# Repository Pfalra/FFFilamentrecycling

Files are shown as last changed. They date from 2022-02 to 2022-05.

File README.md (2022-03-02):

# FFFilamentrecycling

Hello there! This thing is still work in progress. We aim to create a filament converter from 3mm to 1.75mm filament... at least in the short term. In the long term our goal is to design just another filament recycling device that will crack your messed up prints, bottles and any other plastic thing you feed it with.
The mechanical parts are based on the master thesis of one of our contributors. Maybe we will publish his work here too.

Main electronics of our project are a ESP32-WROOM and a MAX10 FPGA reading a CCD sensor. The rest is currently pretty much neglectable as in the future we will integrate everything neatly onto a beautiful PCB instead of the current setup with its off-the-shelf Arduino modules and loads of jumper wire.

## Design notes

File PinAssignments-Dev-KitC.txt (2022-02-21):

INPUTS ONLY:
GPIO34
GPIO35
GPIO36
GPIO39

PINS WITH INTERNAL PULL UP:
GPIO14
GPIO16
GPIO17
GPIO18
GPIO19
GPIO21
GPIO22
GPIO23

PINS WITHOUT INTERNAL PULL UP:
GPIO13          x
GPIO25          x
GPIO26          x
GPIO27          x
GPIO33          x

SERIAL PINS:
GPIO3 (U0RXD) // DEBUG
GPIO1 (U0TXD) // DEBUG

GPIO16 (U2RXD)  x
GPIO17 (U2TXD)  x

I²C:
GPIO21 (SDA)    x
GPIO22 (SCL)    x

VSPI:
GPIO23 (MOSI)   x
GPIO19 (MISO)   x
GPIO18 (CLK)    x
GPIO5 (CS)      x

HSPI:
GPIO13 (MOSI)
GPIO12 (MISO) // Boot fail if pulled high
GPIO14 (CLK) // PWM at boot
GPIO15 (CS) // PWM at boot

BOOTSTRAP PINS:
GPIO0 (DEFAULT PUP) 
GPIO2 (DEFAULT PDOWN)
GPIO5 (DEFAULT PUP) // Outputs PWM at Boot

-----------------------------------------------
ASSIGNMENTS:
FPGA UART-RX    -> GPIO17 v
FPGA UART-TX    -> GPIO16 v

Heater          -> GPIO33 v

SD SPI-SCK      -> GPIO14 v
SD SPI-CS       -> GPIO15 v
SD SPI-MISO     -> GPIO12 v
SD SPI-MOSI     -> GPIO13 v

ADC/OLED I²C-SDA    -> GPIO21   v
ADC/OLED I²C-SCL    -> GPIO22   v

Stepper EN          -> GPIO27 v
ExtStepper STEP     -> GPIO26 v
PullStepper STEP    -> GPIO25 v
WinchStepper STEP   -> GPIO33 v

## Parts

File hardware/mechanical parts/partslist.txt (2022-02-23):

parts list
1. 1x fully assembled All-Metal Hotend Bowden - 3,00 mm
2. 2x MINEBA stepper motor 17PM-K374BN01CN, 1,8°
3. 1x extruder connector
4. 1x extruder mount
5. 1x extrouder mount counterpart 
6. 1x Anself Ultra-quiet Mini DC12V 4.5W Micro Brushless Water Oil Pump
7. 1x PVC tube 9mm
8. 1x PVC tube 6mm
9. 1x tube coupling
10. 1x basin
11. 1x basin cover
12. 1x inlet tube
13. 1x outlet tube
14. 1x MAX1000 - IoT Maker Board 16 kLE, 32 MByte SDRAM
15. 1x Toshiba TCD132D CCD
16. 1x Laser diode 5mW red 650nm 5V
17. 2x 6x24x9mm u-groove bearing
18. 1x 6mm round bar
19. 1x measuring device base
20. 1x measuring device housing
21. 2x bearing mount
22. 2x measuring device spacer
23. 1x FPGA cover
24. 1x laser mount 
25. 2x 6x19x6mm bearing 
26. 1x filament puller connector
27. 1x motor mount
28. 1x motor mount counterpart
29. 2x pull roll
30. 1x filament puller driven gear M=2,5 Z=20 
31. 1x filament puller gear M=2,5 Z=20 
32. 1x motor gear connector
33. 1x MINEBA stepper motor 17PM-K077BP01CN, 1,8°
34. 1x 12mm tube 
35. 1x filament winder driven gear M=2,5 Z=14
36. 1x filament winder gear M=2,5 Z=38
37. 1x filament winder gear counterpart
38. 1x filament winder tube connector
39. 1x filament winder base
40. 1x filament winder stepper motor mount
41. 1x filament winder stepper motor mount counterpart
42. 1x ESP32-Wroom DevKit
43. 1x ADS1115 ADC-Module (HW196)
44. 1x Micro SD-Module (HW125)
45. 1x Voltage Translator Joy-It KY-061
46. 3x A4988 StepStick
47. 1x IRFZ44N MOSFET
48. 3x 47µF Capacitor
49. 1x I^2C OLED Display
50. 1x 100k NTC
51. 2x M2,5 nylon nut DIN934 
52. 2x M2,5 nylon bolt
53. 2x M2 nylon nut DIN934 
54. 2x M2 nylon bolt
55. 8x M3 nut DIN934 
56. 16x M3 bolt 
57. 8x M4 nut DIN934 
58. 8x M4 bolt

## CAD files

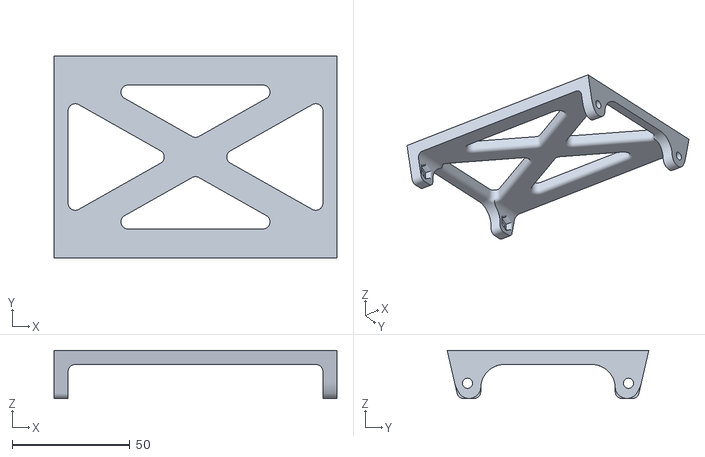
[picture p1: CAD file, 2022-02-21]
hardware/mechanical parts/Grundplatte_Rollenhalter.stl
120.0 x 85.6 x 20.5

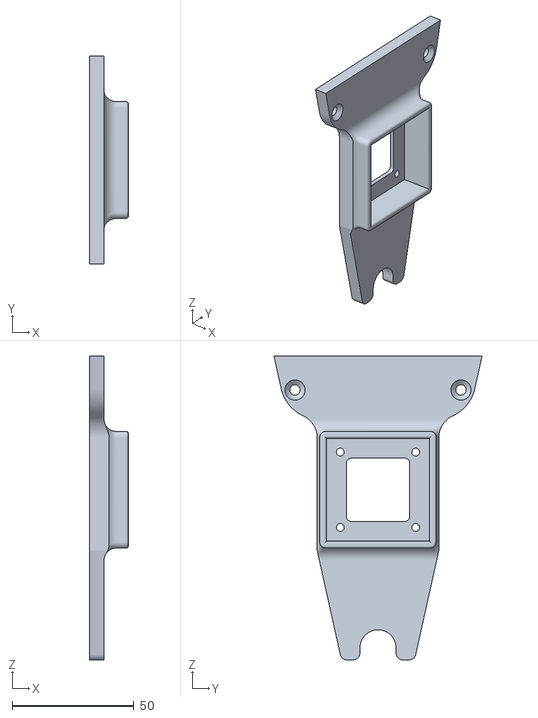
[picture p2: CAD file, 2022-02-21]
hardware/mechanical parts/Halter_Motorseitig.stl
16.0 x 85.6 x 125.0

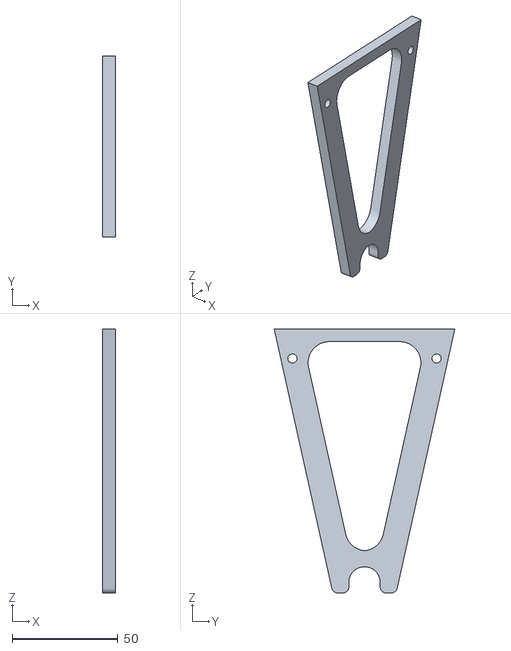
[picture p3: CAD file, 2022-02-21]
hardware/mechanical parts/Halter_Frei.stl
6.00 x 85.6 x 125.0

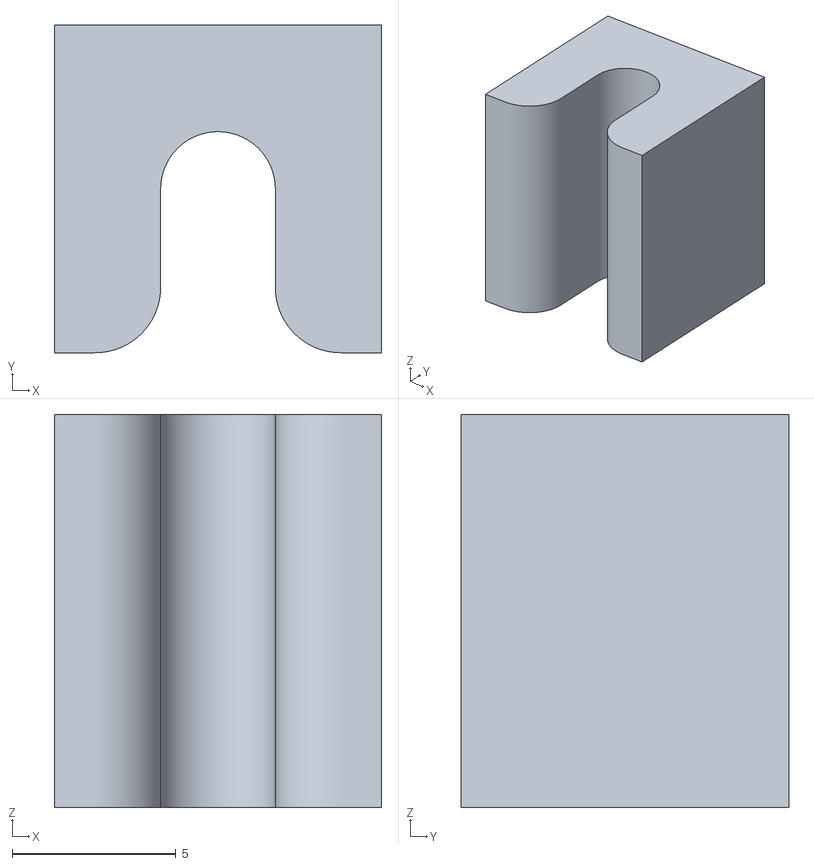
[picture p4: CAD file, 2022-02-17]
hardware/mechanical parts/Distanzstueck.stl
10.00 x 10.0 x 12.0

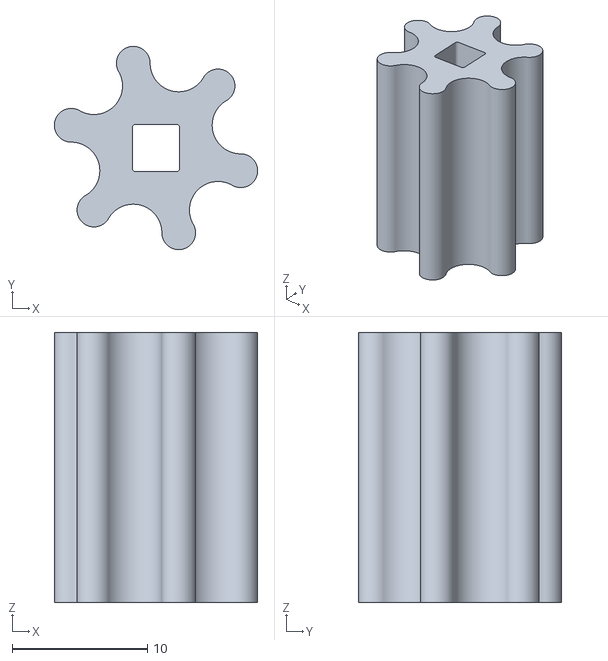
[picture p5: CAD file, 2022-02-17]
hardware/mechanical parts/Kraftschluss Zahnradantrieb.stl
15.1 x 15.1 x 20.0

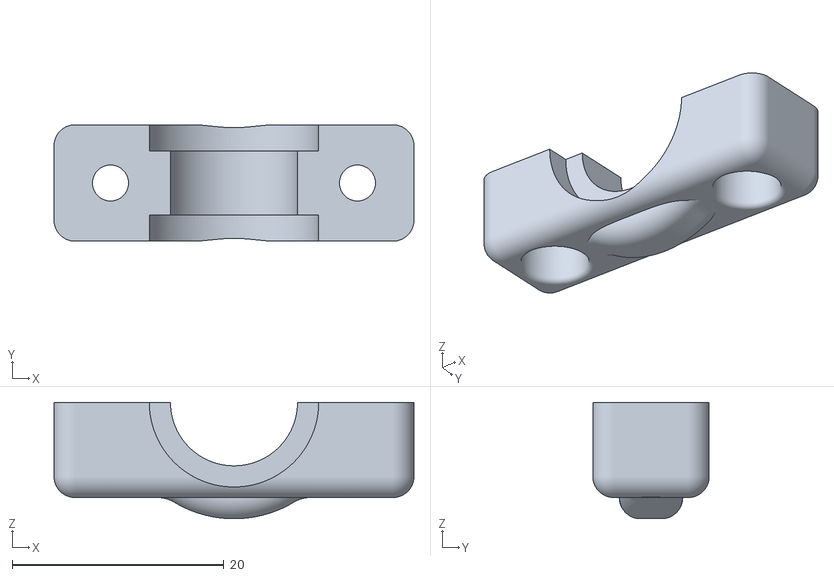
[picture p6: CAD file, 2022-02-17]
hardware/mechanical parts/Gegenstueck Halter.stl
34.0 x 11.0 x 11.0

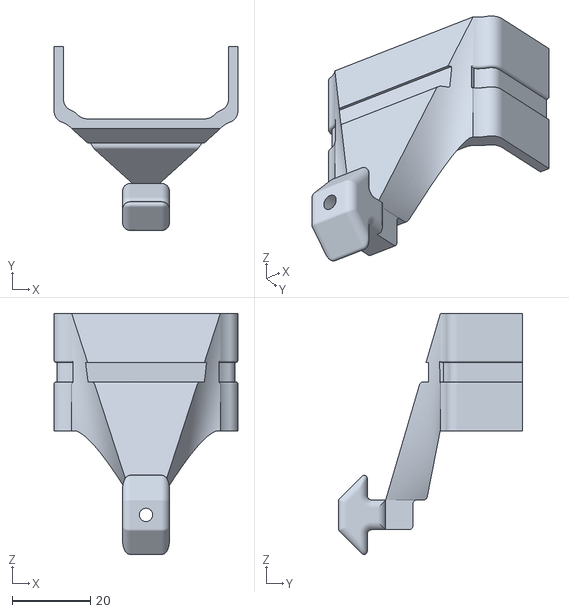
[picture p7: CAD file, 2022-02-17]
hardware/mechanical parts/Extruderhalter.stl
47.0 x 47.0 x 61.6

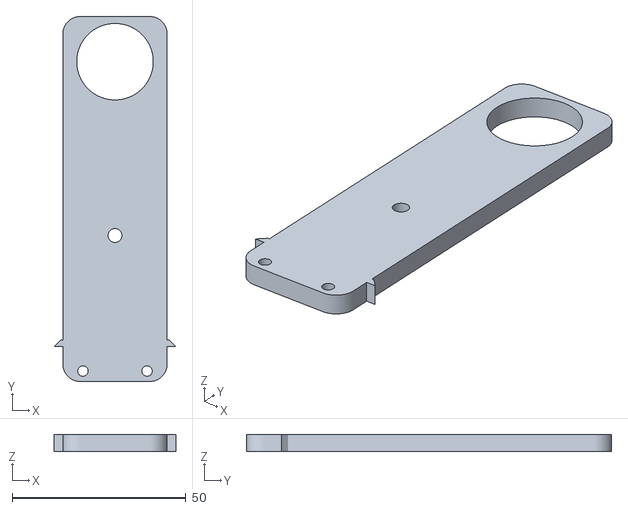
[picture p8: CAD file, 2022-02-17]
hardware/mechanical parts/Motorhalter Gegenstueck.stl
35.0 x 105.0 x 5.00

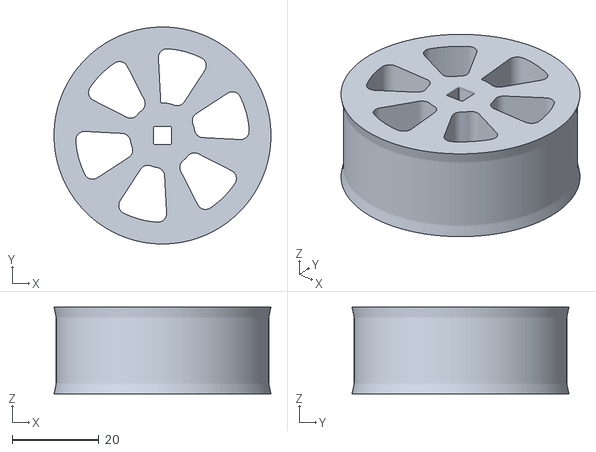
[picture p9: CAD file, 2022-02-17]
hardware/mechanical parts/Ziehrolle.stl
50.0 x 50.0 x 20.0

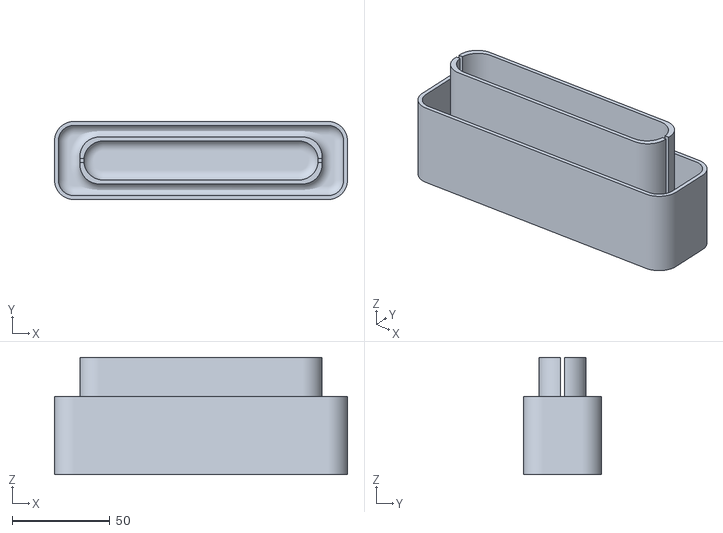
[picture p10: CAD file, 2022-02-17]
hardware/mechanical parts/Wasserbecken.stl
150.0 x 40.0 x 60.0

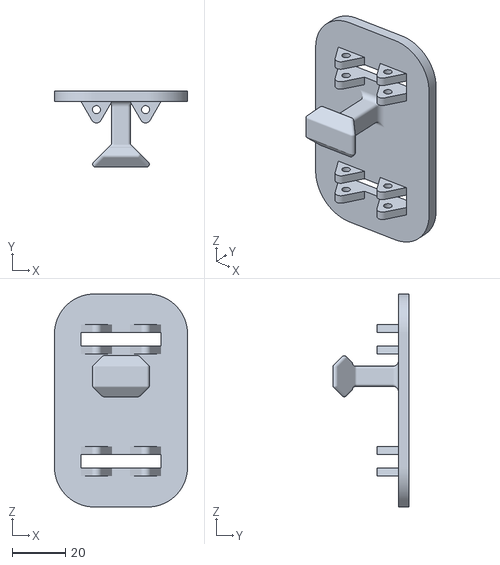
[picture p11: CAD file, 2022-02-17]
hardware/mechanical parts/Grundplatte Item.stl
50.0 x 28.5 x 80.0

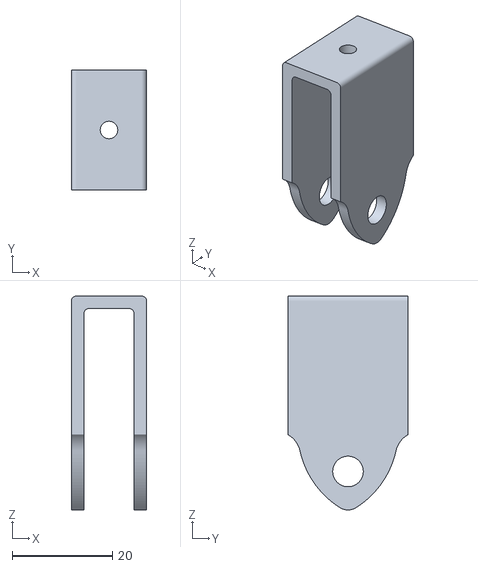
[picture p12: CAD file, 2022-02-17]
hardware/mechanical parts/Kugellagerhalter.stl
15.0 x 24.0 x 42.7

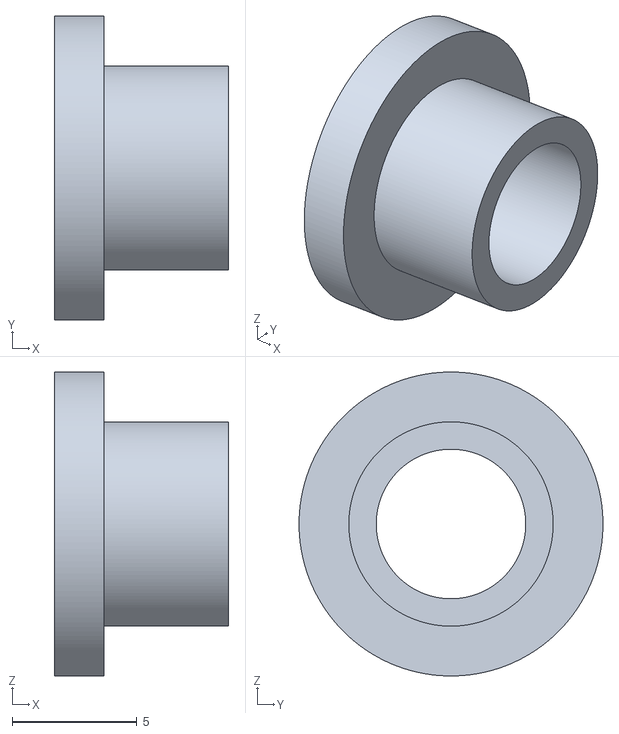
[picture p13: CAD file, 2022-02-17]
hardware/mechanical parts/Kugellageradapter.stl
7.00 x 12.2 x 12.2

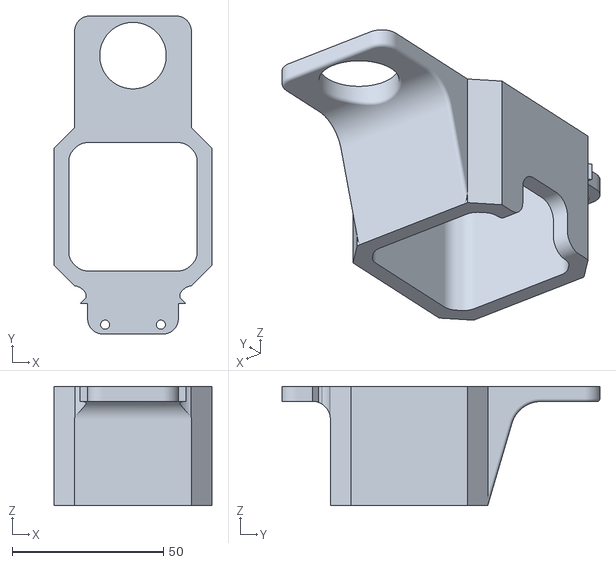
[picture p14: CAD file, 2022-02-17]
hardware/mechanical parts/Motorhalter.stl
52.2 x 105.2 x 39.4

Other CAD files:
FPGA/FilamentSensor/stp.stp
hardware/mechanical parts/Halterplatte.stl
hardware/mechanical parts/Wasserablauf.stl

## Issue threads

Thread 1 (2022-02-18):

UDP runtime error

Pfalra, 2022-02-18:
The udp stack prints an error while listening to the assigned port.
Maybe stack size for the corresponding task is insufficient.

g3gg0, 2022-02-18:
got comparable issues while using ArduinoOTA in some other project.
Stack trace showed the new() call within some UDP receive code was failing.

not sure what causes that.

Pfalra, 2022-02-19:
Up until now we used the Wemos Lolin32. Somehow this error does not occur when the code is running on the ESP32-Wroom DevKit. I just switched the board and additionally to being functional now, we have more pins we can use.

Closed 2022-02-19.

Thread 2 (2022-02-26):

Device cannot be flashed if external modules are powered

Pfalra, 2022-02-26:
Module must be identified and connected to other pins.

Pfalra, 2022-03-08:
This happens as soon as some SD card reader is connected to HSPI. Solution could be initializing SD card after its power line was switched on with a MOSFET or something.

Pfalra, 2022-04-16:
Removed SD module for now. Do not pull Gpio12 high with external modules.

Closed 2022-04-16.

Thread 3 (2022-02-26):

Device falls into reboot loop if I2C communication fails

Pfalra, 2022-02-26:
To recreate the scenario simply the external modules should be powered down. Seems like two tasks want to access the I2C for OLED and ADC and then the device restarts over and over again.

Pfalra, 2022-02-26:
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

g3gg0, 2022-02-26:
so keep ADC and LCD being handled in the same task should work, right?

Pfalra, 2022-02-26:
Yep that should work, However, reading the message in the screenshot above indicates that it can be fixed by calling the yield function while init tries to get the OLED set up should also work out.

Pfalra, 2022-02-27:
Just encountered the following:

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

Either we handle both I²C devices within the same task or we use semaphores to protect the interface. Otherwise this error will happen sporadically. I tend to use the latter suggestion to keep ADC and OLED handling separate.

Closed 2022-04-16.

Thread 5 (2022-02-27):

Unidentified issue in temperature calculation

Pfalra, 2022-02-27:
The temperature calculation sometimes jumps up and down by 10 degC within 500 ms as soon as you touch the thermistor.
After releasing the thermistor the temperature jumps from around 34 deg to 19 deg within 500 ms.
This behaviour indicates a somewhat broken calculation method that needs to be looked into.

g3gg0, 2022-02-27:
What do the raw ADC values tell?

Pfalra, 2022-02-28:
Just checked the raw values. Seems like temperature calculation is messed up. In the near future we are going to use Steinhart-Hart method anyway. So this will no longer be an issue.

Pfalra, 2022-03-03:
Implemented Steinhart-Hart method. Hoever now calculation does not reach more than 28 degrees Celcius. Seems like coefficients are not calculated properly.
Solution could be accepting precalculated coefficients.

Pfalra, 2022-03-06:
Just more or less fixed the temperature calculation. Sometimes it is still a bit jumpy, but that may be due to vcc not being properly stable. I am using caps to filter a bit though. I'll take a look at it with my oscilloscope. However for our purposes jumps of +- 5°C should be acceptable. It may affect viscosity but therefore we have the pid control to mitigate it.

Closed 2022-03-06.

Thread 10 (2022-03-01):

Adaptation of FPGA UART frequency

Pfalra, 2022-03-01:
Currently the FPGA uses something like 5 MBaud for serial com. This might be way too high for the ESP32.

Closed 2022-03-14.

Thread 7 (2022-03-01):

Device crashes when trying to write to SD card

Pfalra, 2022-03-01:
As mentioned in the title. Reason could be that currently log file is opened at app start but only closed once the app is stopped.
The fix should be simple. Open the file in append mode and close it after each line.

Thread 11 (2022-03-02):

PID limits must be set to prevent crashes

Pfalra, 2022-03-02:
If no limits are set the PWM module crashes due to invalid input values for frequency. So set limits for the output values of PID.
Currently best option is to set them in the "InitializeOther" task handler.

tobiornottobinoack, 2022-03-03:
PID limit function was implemented with default values for further actions

Closed 2022-03-03.

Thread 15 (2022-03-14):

Switch FPGA UART output to different pins

Pfalra, 2022-03-14:
FTDI of FPGA could cause issues with current setup so move to the output to other pins.

Closed 2022-04-16.

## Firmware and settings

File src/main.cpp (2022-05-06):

/**************************************************************************************
* \author Raphael Pfaller (raphael.pfaller.dev@googlemail.com)
* \date 02.04.2022
* \note SD functionality is foreseen but was taken out due to technical and timeline 
* problems 
**************************************************************************************/

/* Framework and external libs */
#include <Arduino.h>
#include <SPI.h>
#include <SD.h>
#include <FS.h>
#include <WiFiUDP.h>
#include <math.h>

/* FFF includes */
#include <FFF_Types.h>
#include <FFF_Rtos.h>
#include <FFF_Settings.h>
#include <FFF_Oled.h>
#include <FFF_Adc.h>
#include <FFF_Stepper.h>
#include <FFF_Uart.h>
#include <FFF_Pid.h>
#include <FFF_WiFi.h>
#include <FFF_Heater.h>

const char paramArr[] = "TEMP" DELIMITER \
              "DIAMETER" DELIMITER \
              "PULLMOT_SPD" DELIMITER \
              "EXTMOT_SPD" DELIMITER;

void setup()
{  
  FFF_Uart_init();
  Serial.println();
  Serial.println("FFF Device starting up...");


  /* Initialize WiFi */
  FFF_WiFi_init();

  /* Heater init */
  Serial.println(NL "I>Initializing Heater");
  FFF_Heater_startHeating();

  /* Initialize OLED */
  FFF_Oled_init();
  delay(200);

  /* Initialize ADC */
  Serial.println("\r\nI>Initializing ADC");
  FFF_Adc_init();

  /* Initialize Steppers */
  Serial.println(NL "I>Initializing Steppers");
  FFF_Stepper_init();

  /* Initialize the PID control */
  Serial.println(NL "I>Initializing PID control");
  FFF_Pid_init();
  
  /* Create tasks for initialization */
  Serial.println(NL "Starting InitTasks");
  FFF_Rtos_StartOS();
}


void loop()
{
  TASK_mainControlApp();
}

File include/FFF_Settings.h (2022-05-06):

#ifndef FFF_SETTINGS_H
#define FFF_SETTINGS_H

#include <FFF_Types.h>

/*********************************************************/
/* GENERAL SETTINGS */
/*********************************************************/

#define NL "\r\n"
#define FFF_LOG_FILE_FORMAT ".txt"
#define FFF_VERSION "V0.1"
#define SERIAL0_BAUDRATE 500000 // DEBUG
#define SERIAL2_BAUDRATE 500000 //FPGA
#define DELIMITER ";"
#define FFF_DEVICE_SUPPLY 3.3

/*********************************************************/
/* TEMPERATURE CALUCLATION METHODS */
/*********************************************************/
#define LUT_TRAVERSE_AND_LINEARIZATION 0
#define STEINHART_HART 1

/*********************************************************/
/* TARGET VALUES */
/*********************************************************/
#define TARGET_DIAMETER 1.75


/*********************************************************/
/* THERMISTORS */
/*********************************************************/
#define DUMMY_THERMISTOR 0
#define NTC_3950 1

#define FFF_THERMISTOR0 NTC_3950 // Sets the thermistor 


/*********************************************************/
/* PWM */
/*********************************************************/
#define PWM_HEATER_FREQUENCY    5000



/*********************************************************/
/* TEMPERATURE COEFFICIENTS  */
/*********************************************************/
#define TEMPERATURE_CALC_METHOD STEINHART_HART_METHOD
#define NORM_TEMP   25.0
#define NORM_RES    100000.0

// The following coefficients were calculated with the NTC 
// calculator at 
#define ALPHA_COEFF -0.0559
#define BETA_COEFF 3950

/*********************************************************/
/* ANALYZER */
/*********************************************************/
// 1093 PIXs
#define MEANFILTER_ACTIVE       TRUE
#define MEANFILTER_WEIGHT_COEFF 10
#define DIAMETER_SCALING_COEFF  1
#define MEASUREMENT_LENGTH      1100
#define FIRST_DEAD_PIX          64
#define LAST_DEAD_PIX           20
#define SYNC_LENGTH             4
#define DIA_MEAS_HYST           2

/*********************************************************/
/* OLED */
/*********************************************************/
#define OLED_ADDR 0x3C
#define OLED_WIDTH_PX 128
#define OLED_HEIGHT_PX 64
#define OLED_MAX_CHARS 24


/*********************************************************/
/* DUMMY VALUES */
/*********************************************************/
#define DUMMY_VAL_TEMPERATURE 333
#define DUMMY_VAL_DIAMETER 1.75
#define DUMMY_VAL_EXTMOT_SPEED 100
#define DUMMY_VAL_PULLMOT_SPEED 300
#define EXTRUDE_RATE_STEPS_PS 42


/*********************************************************/
/* ADC */
/*********************************************************/
#define EXT_ADC_ADDR 0x48
#define EXT_ADC_TEMP_CHANNEL 3
#define MAX_TEMP_DELTA_DEG  25.0


/*********************************************************/
/* PID */
/*********************************************************/
#define KP_PULL_MOT_DEFAULT 1.0
#define KI_PULL_MOT_DEFAULT 1.0
#define KD_PULL_MOT_DEFAULT 1.0


/*********************************************************/
/* UDP */
/*********************************************************/
#define UDP_PORT 666 // Doom intensifies
#define UDP_PBUF_SIZE 255
#define UDP_CONFIRM "OK" NL

#define UDP_APP_START_CMD "START"
#define UDP_APP_STOP_CMD "STOP"
#define UDP_APP_PAUSE_CMD "PAUSE"
#define UDP_APP_LIST_CMD "LIST"
#define UDP_SET_EXTRUDER_SPEED_CMD "EX"
#define UDP_SET_PULLER_SPEED_CMD "PU"
#define UDP_SET_WINCH_SPEED_CMD "WI"

#define UDP_START_CONFIRM "STARTING APP" NL
#define UDP_STOP_CONFIRM "STOPPING APP" NL
#define UDP_PAUSE_CONFIRM "PAUSING APP" NL



/*********************************************************/
/* PIN ASSIGNMENTS AND HARDWARE */
/*********************************************************/
#define THERMISTOR_PULL_UP_VAL 4700.0f
#define STEPPER_MICROSTEPS  16

// #define HEATER_OUTPUT_PIN   33
#define RX_TO_FPGA_PIN      16
#define TX_TO_FPGA_PIN      17
#define OLED_SCL_PIN        22
#define OLED_SDA_PIN        21
#define STEPPER_EN_PIN      27
#define EXTRUDER_STEP_PIN   26
#define PULLER_STEP_PIN     25
#define WINCH_STEP_PIN      33
#define HEATER_OUTPUT_PIN   14
#define EMERGENCY_BUTTON_PIN 36



/*********************************************************/
/* TASK INTERVAL SETTINGS */
/*********************************************************/
#define UDP_HANDLE_INTERVAL_MS              400
#define LOG_INTERVAL_MS                     500
#define PID_TEMP_INTERVAL_MS                1000
#define PID_DIAMETER_INTERVAL_MS            1000
#define FPGA_CALCULATE_DIAMETER_INTERVAL_MS 1000
#define ADC_SAMPLE_INTERVAL_MS              500
#define OLED_REFRESH_INTERVAL_MS           400
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

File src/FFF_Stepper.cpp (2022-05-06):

#include <Arduino.h>
#include <FFF_Stepper.h>
#include <FFF_Settings.h>
#include <FFF_Types.h>
#include <FFF_Pwm.h>


FFF_PwmHandle extruderPwm = 
{
  0,                  // id
  EXTRUDER_STEP_PIN,  // outputPin
  0,                  // channel
  FFF_PWM_RES_1BIT,   // resolution
  50.0,                // dutyCycle in percentage
  0.0                 // frequency
};

FFF_Stepper extruderStepper = 
{
  0,                  // id
  EXTRUDER_STEP_PIN,  // stepPin
  STEPPER_MICROSTEPS, // microsteps
  &extruderPwm,       // pwmPtr
  1.0
};


FFF_PwmHandle pullPwm = 
{
  1,                  // id
  PULLER_STEP_PIN,    // outputPin
  0,                  // channel
  FFF_PWM_RES_1BIT,   // resolution
  50.0,                // dutyCycle in percentage
  0.0                 // frequency
};

FFF_Stepper pullStepper = 
{
  1,                  // id
  PULLER_STEP_PIN,    // stepPin
  STEPPER_MICROSTEPS, // microsteps
  &pullPwm,           // pwmPtr
  1                   // gearRatio
};


FFF_PwmHandle winchPwm = 
{
  2,                  // id
  PULLER_STEP_PIN,    // outputPin
  0,                  // channel
  FFF_PWM_RES_1BIT,   // resolution
  50.0,                // dutyCycle in percentage
  0.0                 // frequency
};

FFF_Stepper winchStepper = 
{
  2,                  // id
  WINCH_STEP_PIN,     // stepPin
  STEPPER_MICROSTEPS, // microsteps
  &winchPwm,          // pwmPtr
  2.7143              // gearRatio
};


void FFF_Stepper_init()
{
  pinMode(STEPPER_EN_PIN, OUTPUT);

  FFF_Stepper_disableAll();

  pinMode(EXTRUDER_STEP_PIN, OUTPUT);
  pinMode(PULLER_STEP_PIN, OUTPUT);
  pinMode(WINCH_STEP_PIN, OUTPUT);

  FFF_Pwm_init(&extruderPwm);
  FFF_Pwm_stopOutput(&extruderPwm);
  FFF_Pwm_init(&pullPwm);
  FFF_Pwm_stopOutput(&pullPwm);
  FFF_Pwm_init(&winchPwm);
  FFF_Pwm_stopOutput(&winchPwm);

  FFF_Stepper_disableAll();
}


void FFF_Stepper_enableAll()
{
  digitalWrite(STEPPER_EN_PIN, LOW);
}


void FFF_Stepper_disableAll()
{
  digitalWrite(STEPPER_EN_PIN, HIGH);
}


void FFF_Stepper_runStepsPerSecond(FFF_Stepper* stepperPtr, double stepsPerSecond)
{
  stepperPtr->pwmPtr->freq = stepsPerSecond;
  FFF_Pwm_changeFrequency(stepperPtr->pwmPtr);
}


void FFF_Stepper_stop(FFF_Stepper* stepperPtr)
{
  FFF_Pwm_stopOutput(stepperPtr->pwmPtr);
}


void FFF_Stepper_stopAll()
{
  FFF_Stepper_stop(&extruderStepper);
  FFF_Stepper_stop(&pullStepper);
  FFF_Stepper_stop(&winchStepper);
}


double FFF_Stepper_getWinchStepperSpeed()
{
  return winchStepper.gearRatio*winchPwm.freq;
}


double FFF_Stepper_getPullStepperSpeed()
{
  return pullStepper.gearRatio*pullPwm.freq;
}


double FFF_Stepper_getExtruderStepperSpeed()
{
  return extruderStepper.gearRatio*extruderPwm.freq;
}

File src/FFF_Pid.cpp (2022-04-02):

#include <Arduino.h>
#include <FFF_Pid.h>
#include <FFF_Settings.h>
#include <FFF_Temperature.h>
#include <FFF_Stepper.h>


TaskHandle_t PIDDiameterTaskHandle;
TaskHandle_t PIDTemperatureTaskHandle;

/* Filament control */
double filDiameterMm = 0.0;
double targetDiameterMm = TARGET_DIAMETER;
double pwmFrequency = 0.0;

double kp_mot = KP_PULL_MOT_DEFAULT; 
double ki_mot = KI_PULL_MOT_DEFAULT;
double kd_mot = KP_PULL_MOT_DEFAULT;

PID pidMotControl(&filDiameterMm, &pwmFrequency, &targetDiameterMm, kp_mot, ki_mot, kd_mot, AUTOMATIC);

/* Temperature control */
double hotendTemp = 0.0;
double pwmDutyCycle = 20.0;
double targetTemp = 215.0;

double kp_temp = 24.4;
double ki_temp = 1.4;
double kd_temp = 106.8;

PID pidTempControl(&hotendTemp, &pwmDutyCycle, &targetTemp, kp_temp, ki_temp, kd_temp, AUTOMATIC);





void FFF_Pid_init()
{
  // set outputlimits for PID
  pidMotControl.SetOutputLimits(0.0, 1000.0);
  pidTempControl.SetOutputLimits(0.0, 100.0);
}

void TASK_handleDiameterMotorPID(void *param)
{
  while (1)
  {
    // pidMotControl.Compute();
    // Provide the values to the steppers 
    
    // send data only when you receive data:
  //if (Serial2.available() > 0) {
    // read the incoming byte (should be the FPGA input?):
    //incomingByte = Serial2.read();

    if (pwmFrequency <= 0.0)
    {
      pwmFrequency = 50;
    }
    FFF_Stepper_runStepsPerSecond(&pullStepper, pwmFrequency);
    FFF_Stepper_runStepsPerSecond(&winchStepper, pwmFrequency);
    vTaskDelay(PID_DIAMETER_INTERVAL_MS);
  }
}


void TASK_handleTempPID(void *param)
{
  while (1)
  {
    pidTempControl.Compute();
    // Provide the values to the heaters 

    vTaskDelay(PID_TEMP_INTERVAL_MS);
  }
}


TaskHandle_t* FFF_Pid_getDiameterTaskHandle()
{
    return &PIDDiameterTaskHandle;
}


TaskHandle_t* FFF_Pid_getTemperatureTaskHandle()
{
    return &PIDTemperatureTaskHandle;
}

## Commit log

2022-02-16 Fixed issues regarding TaskHandles+settings and started implementing task control
    [FFF_Settings.h, main.cpp]
2022-02-16 First UDP implemetation with RT errors in parsePacket
    [FFF_Settings.h, main.cpp]
2022-02-17 Added mechanical parts
    [Distanzstueck.stl, Extruderhalter.stl, Gegenstueck Halter.stl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]
2022-02-19 Added preliminary pin assignment textfile for ESP32 WROOM DevKit and adjusted platformio config
2022-02-19 Updated the pin assignment in the settings and added notes to the pin assignment txt-file
2022-02-21 Added Filamentwinder parts
    [Grundplatte_Rollenhalter.stl, Halter_Frei.stl, Halter_Motorseitig.stl]
2022-02-23 Added ADC temperature read to its handle and rudimentary task control via UDP.
2022-02-25 Added motorspeed as output line on OLED.
2022-02-25 Added untested temperature lookup function to ADC code and adapted its init.
2022-02-25 Extracted stepper module.
2022-02-26 Fixed an error regarding stepper enablement and added bit more debug output to main.
    [FFF_Stepper.cpp, main.cpp]
2022-02-26 Fixed and added OLED output
    [FFF_Oled.cpp, FFF_Settings.h]
2022-02-26 Added thermistor lookup table and moved temperature analysis to main.
2022-02-26 Fixed thermistor LUT assignment.
2022-02-26 Reimplemented the temperature lookup function. It is not tested yet.
2022-02-26 Fixed embarrassing errors in temperature calculation and adapted OLED output accordingly.
    [FFF_Adc.cpp, FFF_Oled.cpp, FFF_Settings.h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]
2022-02-27 Did a lot of restructuring and implemented proper logging. The latter however causes guru meditation error.
    [FFF_Oled.cpp, FFF_Sd.cpp, FFF_Settings.h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]
2022-02-28 Added some log files and changed PIO config for esp32 exception decoder
2022-02-28 Implemented pwm module and adjusted stepper and heater accordingly. <untested>
2022-02-28 Added debug switch for ADC after checking raw values.
2022-03-01 Removed non-functional part in thermistor.c, deactivated steppers due to exceptions and implemented proper OLED output.
2022-03-01 Adapted the main code to just let the pull motor spin and use pwm. No pid control is currently done as it causes crashes.
    [FFF_Settings.h, main.cpp]
2022-03-02 Added gear ratio to stepper structure.
2022-03-03 Implemented PID output limits
2022-03-03 Fixed the setting of output limits for the pid controllers.
    [main.cpp]
2022-03-05 Implemented a somewhat functional Steinhart-Hart temperature calculation.
2022-03-11 Fixed some minor issues in main and added code to let the steppers spin at constant speed after START CMD
    [FFF_Adc.cpp, FFF_Settings.h, main.cpp]
2022-03-18 leave STP enabled else we get some clock issues
    [stp.stp]
2022-03-27 Started implementation of fpga reading via uart2
2022-04-02 Did a major cleanup. Some issues still need fix.
    [FFF_Pid.cpp, FFF_Rtos.cpp, FFF_Sd.cpp]
2022-04-02 Fixed lot of issues and brought them down to some linker errors.
    [FFF_Rtos.cpp, FFF_Settings.h, FFF_Temperature.c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]
2022-04-03 Implemented FPGA sensor readout. Not tested. Diameter analysis needs reimplementation.
2022-04-05 Fixed issues in UART interrupt execution
    [FFF_DiaAnalyzer.cpp, FFF_Settings.h, FFF_Uart.cpp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]
2022-04-05 Fixed OLED display issues and traps due to i2c blocking
    [FFF_Oled.cpp, FFF_Rtos.cpp, FFF_Settings.h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]
2022-04-15 Fixed minor issues and added code for SYNC reception validation
    [FFF_Rtos.cpp, FFF_Uart.cpp, FFF_WiFi.cpp]
2022-05-06 Fixed multiple issues incl. heater. Filament diameter readout issue handling still pending.
    [FFF_DiaAnalyzer.cpp, FFF_Heater.cpp, FFF_Oled.cpp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]
